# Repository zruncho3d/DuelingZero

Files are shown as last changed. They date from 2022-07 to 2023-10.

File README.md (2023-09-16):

## Dueling Zero - a Dual Gantry V0 mod

**Two extruders.  No compromises.**

Enable dual-color, dual-material, and dual-part printing... with the same speed and quality as single-extruder printing.

Mod a [Voron Zero](https://vorondesign.com/voron0.2) or build one fresh!

**D0** is the only open-source, fully-documented, reproducible-by-anyone Dual Gantry printer out there.

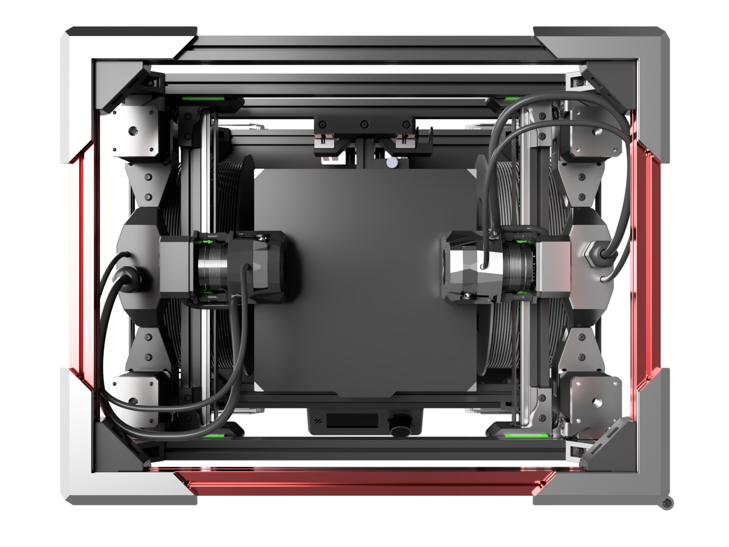
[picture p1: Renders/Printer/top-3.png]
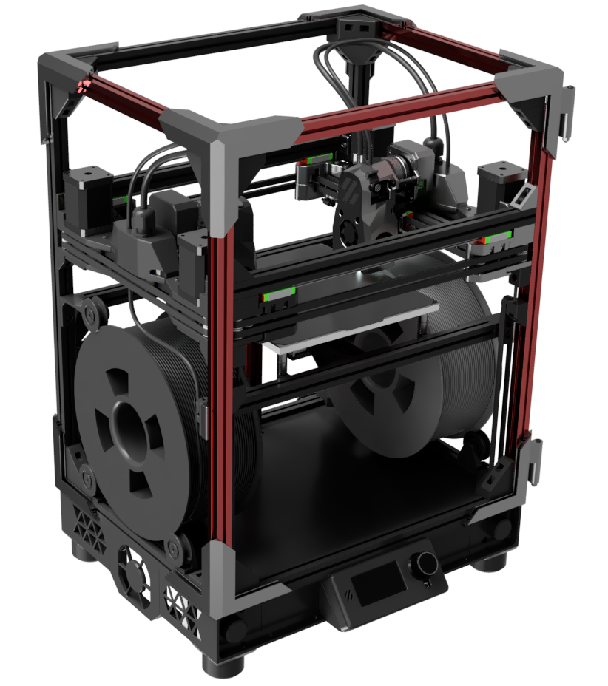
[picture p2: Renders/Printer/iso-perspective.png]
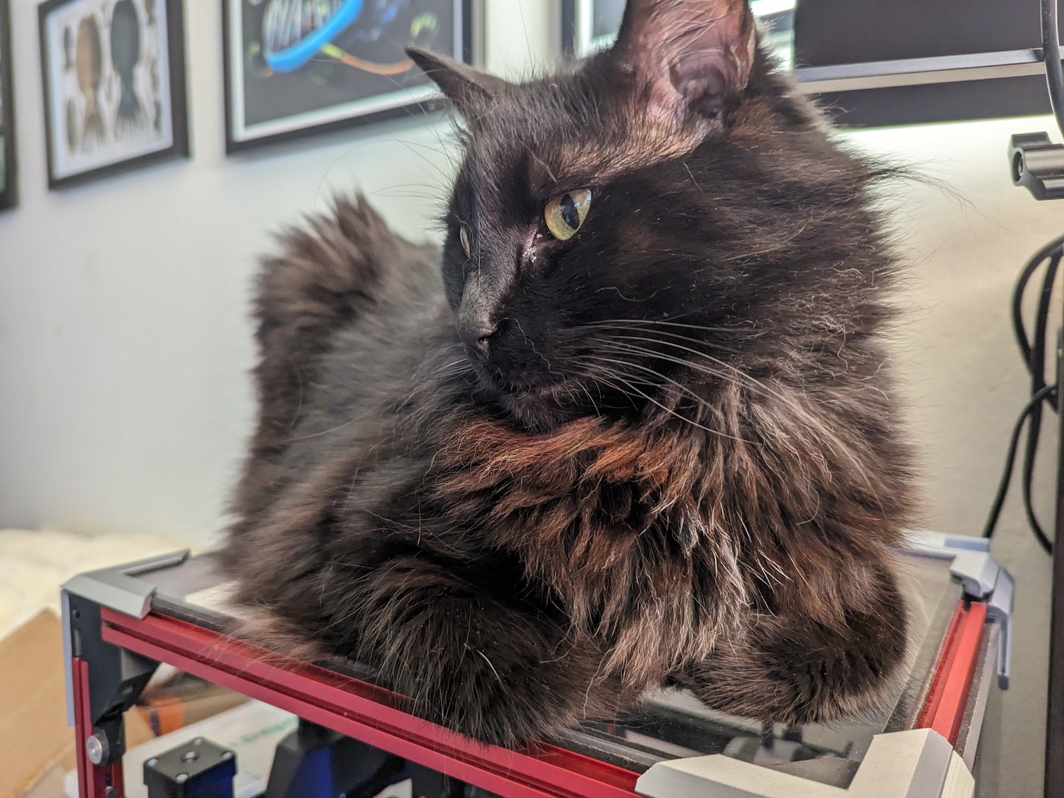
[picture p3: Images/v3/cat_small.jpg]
|  |  | 
| - | - | - |

In a Dual Gantry printer, the two heads are *fully* independent.  With **no extra weight** to drag around (vs an IDEX printer), and **no complexity added** to switch between heads (vs a toolchanger), Dual Gantry is a promising way to do more with a 3D printer.

Curious?  Watch the first one print below!

# [> > > Watch Video from first prints](https://youtu.be/2YI3_g30EwA)

(https://youtu.be/2YI3_g30EwA)
(original v1 gantry shown)

## What's Here?

Tons of content.  On this page:

- #### [Releases](#releases): Visual release notes
- #### [Overview](#overview): Why Dual Gantry?
- #### [Sample Builds](#samplebuilds): Parts and sizes
- #### [Links](#links), [Credits](#credits), and [Support](#support)

... and beyond, split into their own pages:
- #### [Parts](PARTS.md): Parts list to build your own
- #### [Instructions](INSTRUCTIONS.md): Instructions to print, assemble, and configure
- #### [Software](SOFTWARE.md): Two toolheads in one workspace, explained
- #### [FAQ](FAQ.md): Common questions, answered
- #### [Archived v1](Archived-v1/REAMDE-v1.md): Prior design

**Enjoy!** I hope this project inspires you to build something new, whether a D0 or your own design.  -Z

## Releases

**2023-09-16 v3 Gantry release and updates**

This release moves to a completely-new, symmetric, nested belt path:

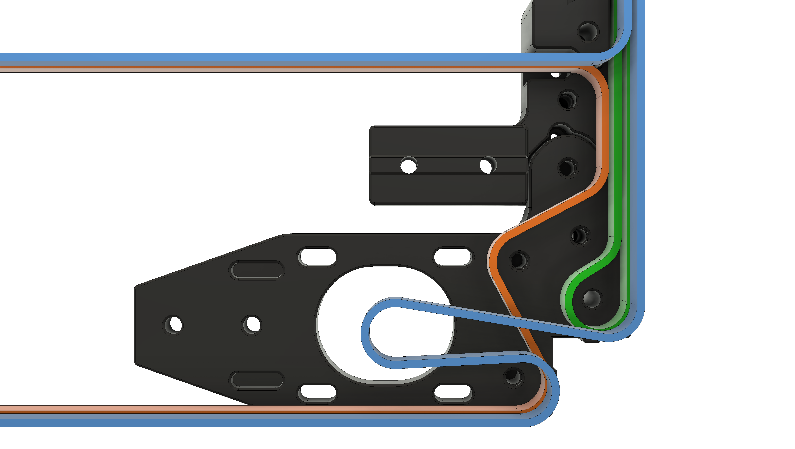
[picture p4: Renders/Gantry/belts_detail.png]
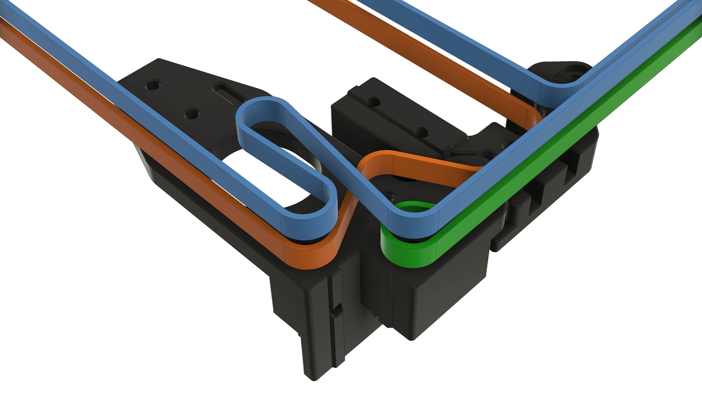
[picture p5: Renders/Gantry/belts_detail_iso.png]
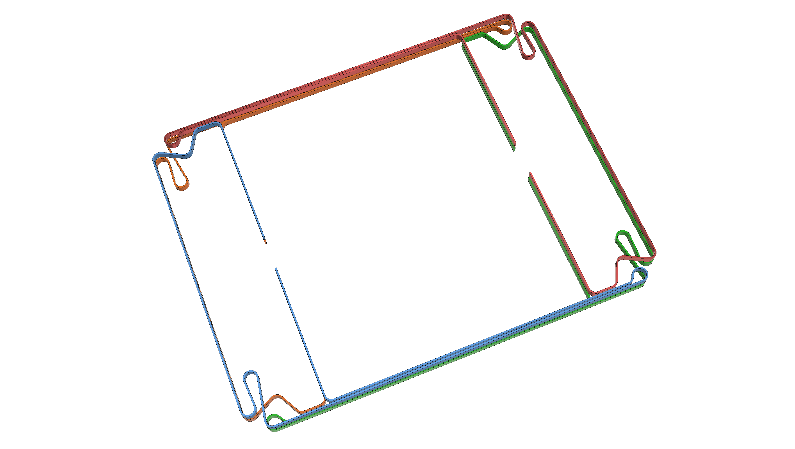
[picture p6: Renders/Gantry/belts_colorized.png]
|  |  |  |
| - | - | - |

The new [Pandora's Box](https://github.com/MasturMynd/Pandoras_Box/tree/main)-derived gantry design, created in close collaboration with `Desune` on Discord, has far fewer unique parts, adds travel, and enables wider toolhead compatibility.

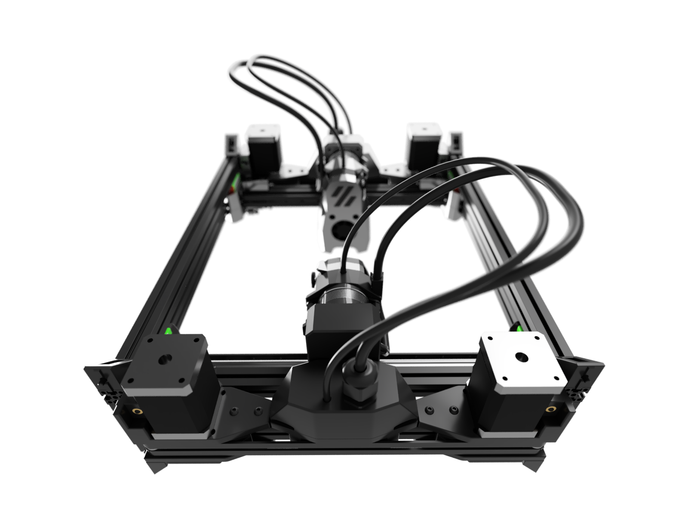
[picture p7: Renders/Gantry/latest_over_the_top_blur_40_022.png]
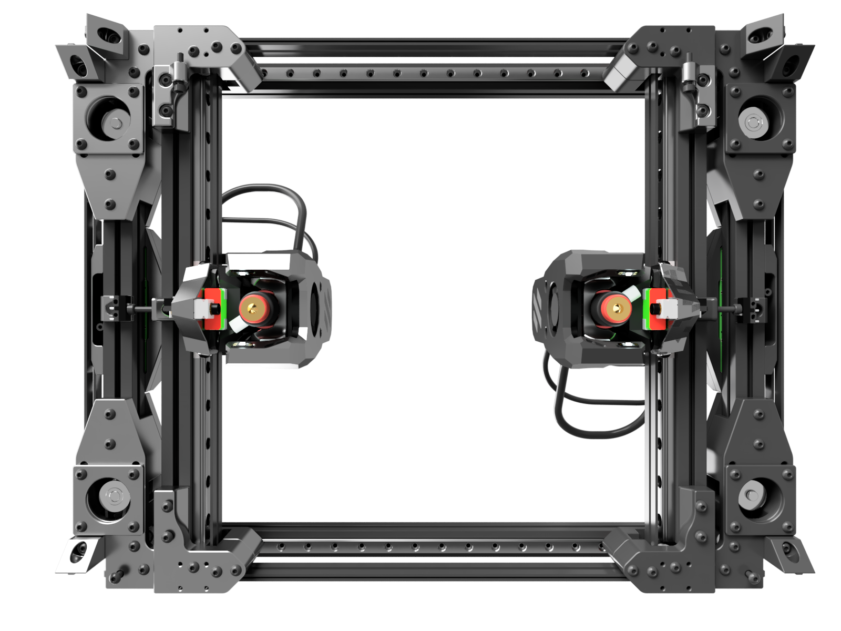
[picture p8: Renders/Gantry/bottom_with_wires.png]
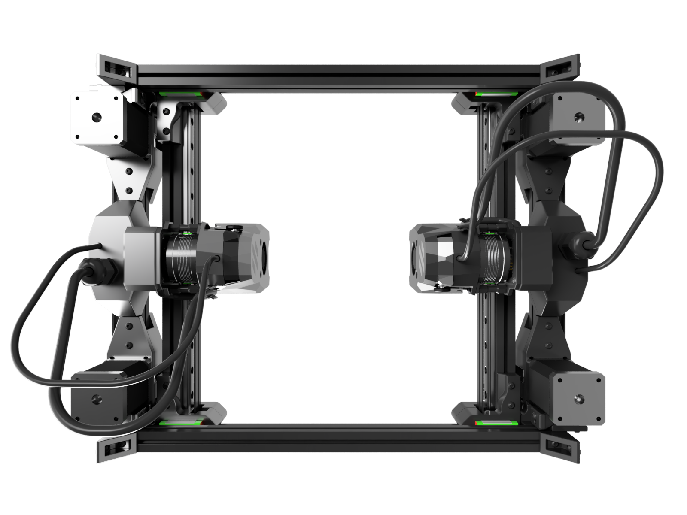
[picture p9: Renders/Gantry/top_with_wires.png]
|  |  |  |
| - | - | - |

Here's the side-by-side comparison from above, with v1 on left, and new v3 on right:

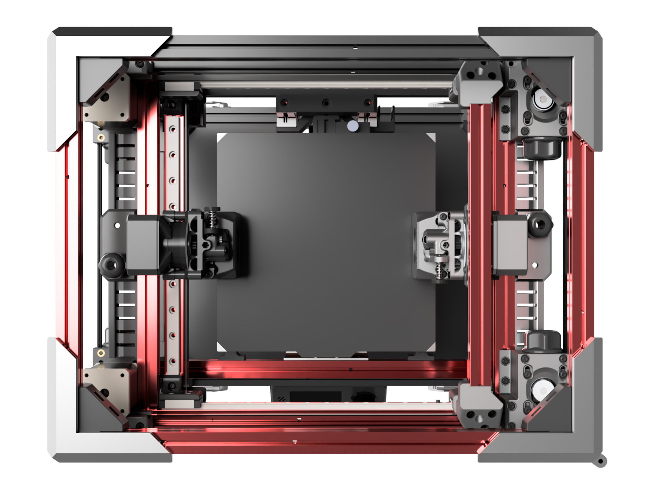
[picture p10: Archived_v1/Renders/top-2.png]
|  |  |
| - | - |

Or, in reality:

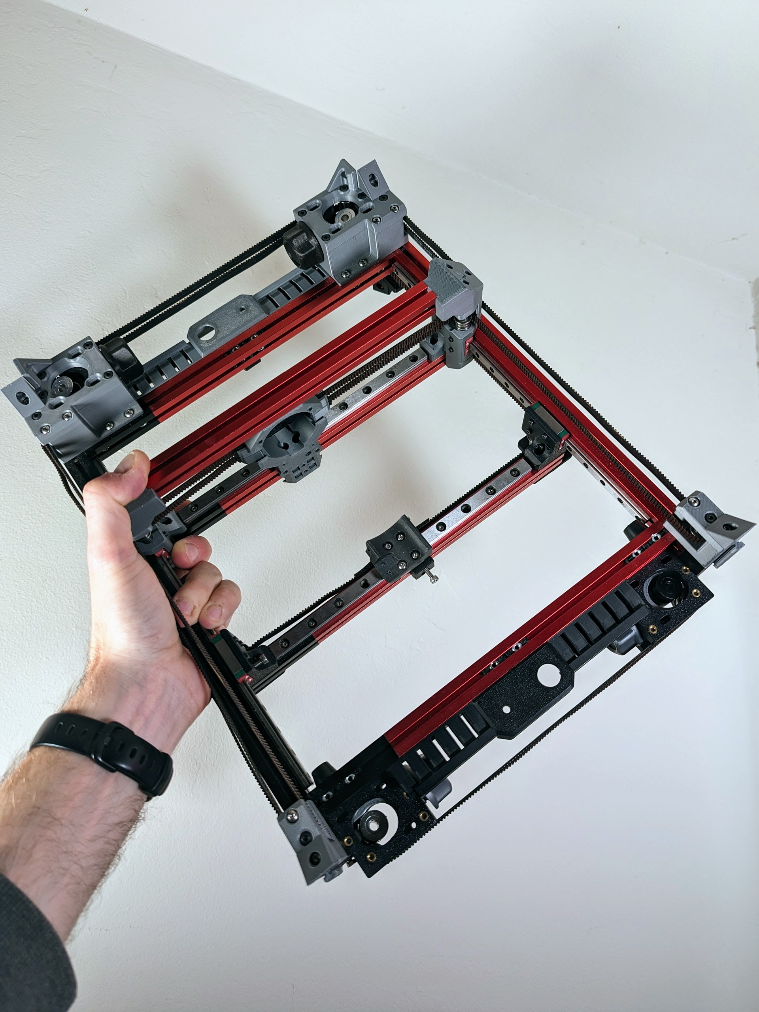
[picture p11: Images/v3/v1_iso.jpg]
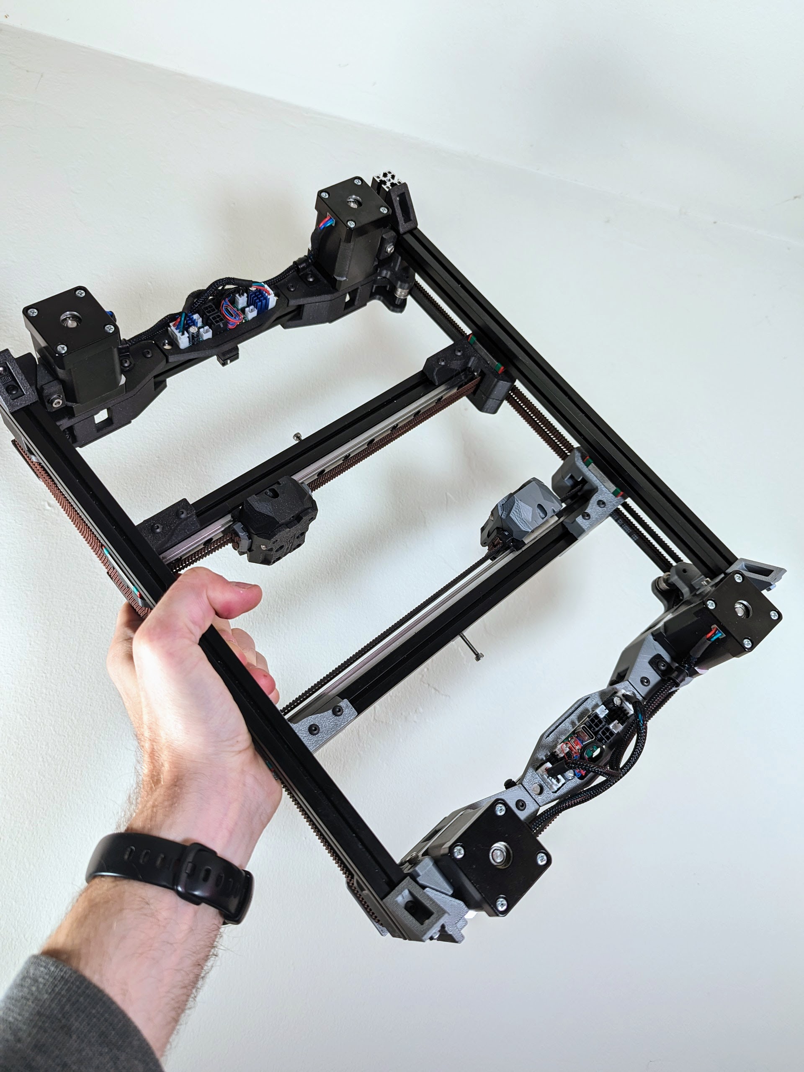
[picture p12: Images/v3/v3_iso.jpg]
|  |  |
| - | - |

The printer looks a little different now, with internal spool holders!

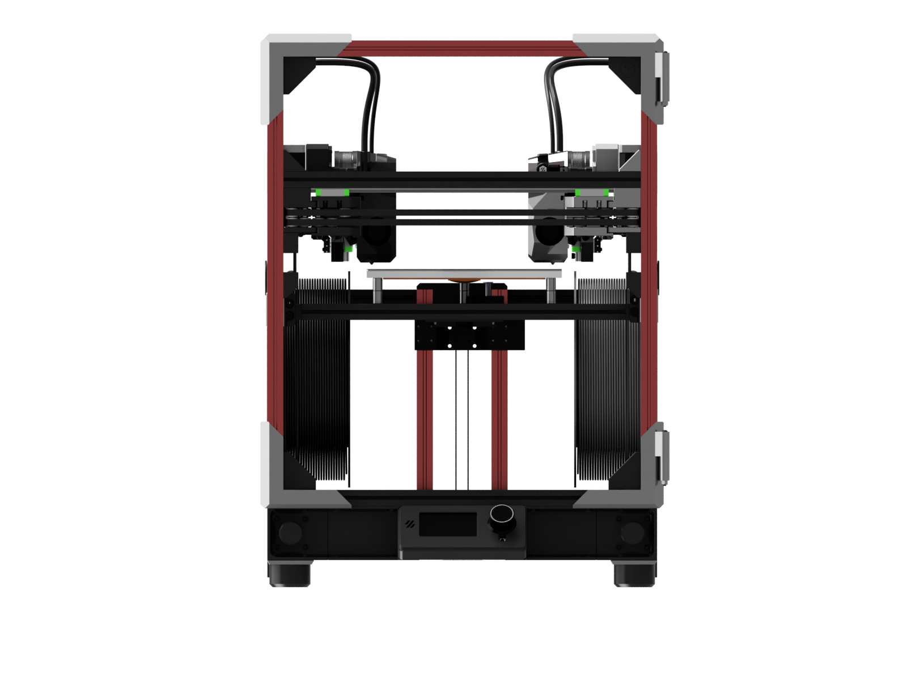
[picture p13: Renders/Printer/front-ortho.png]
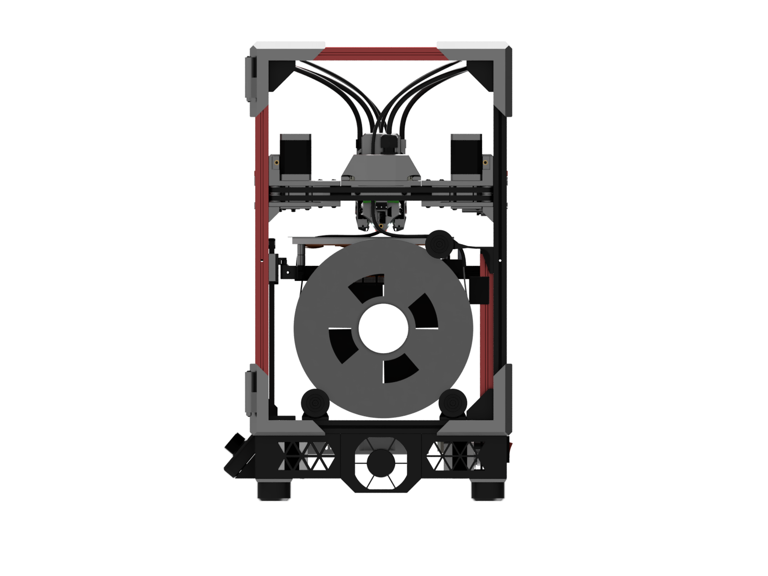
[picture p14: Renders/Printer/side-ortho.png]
|  |  |  |
| - | - | - |

In short - **this is a big update**.  *This is what D0 should have always been.*

Sometimes it's only through iteration and collaboration that you get to what feels right.  **The v3 gantry feels right**. No weird strut, no flipped motors, smaller, more maintainable... all-around, better.  See the comparison table on the [Design](DESIGN.md) page for more details on why.

Other improvements:
* **Boop support** for perfect first layers every time, nozzle probing with [Boop](https://github.com/PrintersForAnts/Boop) is now the default.  There are no magnets to get loose in a heated chamber and no probe motions to configure anymore.
* **Better toolhead compatibility**, including a Voron 0.2-compatible mount for the Voron Mini Stealthburner toolhead and many others.
* **Gantry board support** for the [GBB15 gantry board](https://github.com/skuep/GBB15) - enables super-clean, easy wiring with magnetic-attach covers.
* **Dual internal spool holders** added, reducing the effective width.

**Existing v1 builders**: to upgrade, the main costs will be new rails, a few new extrusions, and Boop parts.  There's nothing wrong with your v1 build; it will print fine.  But  if you want more travel and the benefits of Boop, a fresh rebuild with the new larger default frame size might make sense.

**For earlier releases**, see the [Updates](updates.md) page.

## Overview

### What’s a Dual Gantry printer?

**Dual Gantry** is a rare 3D printer type with two toolheads moved by **two** *completely independent* XY motion systems:

 

Yes, you’re seeing double, with black and silver toolheads in a dual-CoreXY motion configuration.

### Why a Dual Gantry printer?

In general, a second hotend adds enormous flexibility - to support two colors, two materials (typically support + main), and two nozzle sizes, in one print, with no color-bleed issues, cross-contamination, or wasteful purging.  Sounds good, right!

Well, that second hotend, if mounted on a single toolhead, can get in the way of print quality, as it drools filament when not in use - and the toolhead is now custom. :frowning:

So along comes IDEX, short for Independent Dual Extrusion, which adds a second, independent toolhead on a shared axis (typically the X axis).  Sounds better, right?

No drool, plus something cooler: one printer can now print two identical parts simultaneously, in mirror or duplicate modes. :muscle:  (note: in theory; depends on firmware support)

Open-source IDEX designs include [Voron](https://vorondesign.com/)-derived ones, like [Zruncho](https://github.com/zruncho3d)’s [Double Dragon](https://github.com/zruncho3d/double-dragon), [Eddietheengineer](https://www.youtube.com/eddietheengineer)'s [Tridex](https://github.com/FrankenVoron/Tridex/), and [Ankurv](https://github.com/ankurv2k6)’s [IDEX Switchwire](https://github.com/ankurv2k6/voron_idex_switchwire).  There's also the [Muldex](https://github.com/3dprintingworld/MULDEX), and there's no shortage of commercial examples, too: [Sovol SV04](https://sovol3d.com/products/sv04), [FlashForge Creator Pro](https://www.flashforge.com/product-detail/flashforge-creator-pro-2-3d-printer), [BCN Sigma](https://www.bcn3d.com/bcn3d-sigma-d25/), [Jadelabo J1](https://www.jadelabo.com/), and many more.

But that second toolhead comes at a cost: moving mass, which has effects on print speed (max accel) and quality (typically, ringing artifacts).  :neutral_face:

> Simplify, then add lightness - [famous quote from Colin Chapman at Lotus](http://www.lotuscars.com.tr/about-us/lotus-philosophy/index-31332.html#:~:text=At%20the%20root%20of%20our,was%20another%20of%20Chapman's%20premises.)

Whether building a fast race car or a fast printer, physics can't be ignored.  

You can mitigate the moving mass somewhat, by using a lighter toolhead, typically with a remote Bowden extruder, but Bowden extruders introduce their own tuning challenges.

**With Dual Gantry, you get a no-mass-added gantry for the common case of single-extruder prints.**  Unlike an IDEX, here, each toolhead is *truly independent* and can move in X *and* Y on its own - [potentially to print two completely different objects at once!](https://forum.duet3d.com/topic/27895/beta-testers-for-multiple-motion-system-support)

There’s no hit to max acceleration or potential for ringing caused by dragging around a heavy second toolhead on a longer rail all the time.

Sure, you can't print more than two colors, like a multi-material unit or toolchanger can, but everything in engineering is tradeoffs... and Dual Gantry is an interesting and new point in the broader space of 3D printer types that support multiple extrusion:  

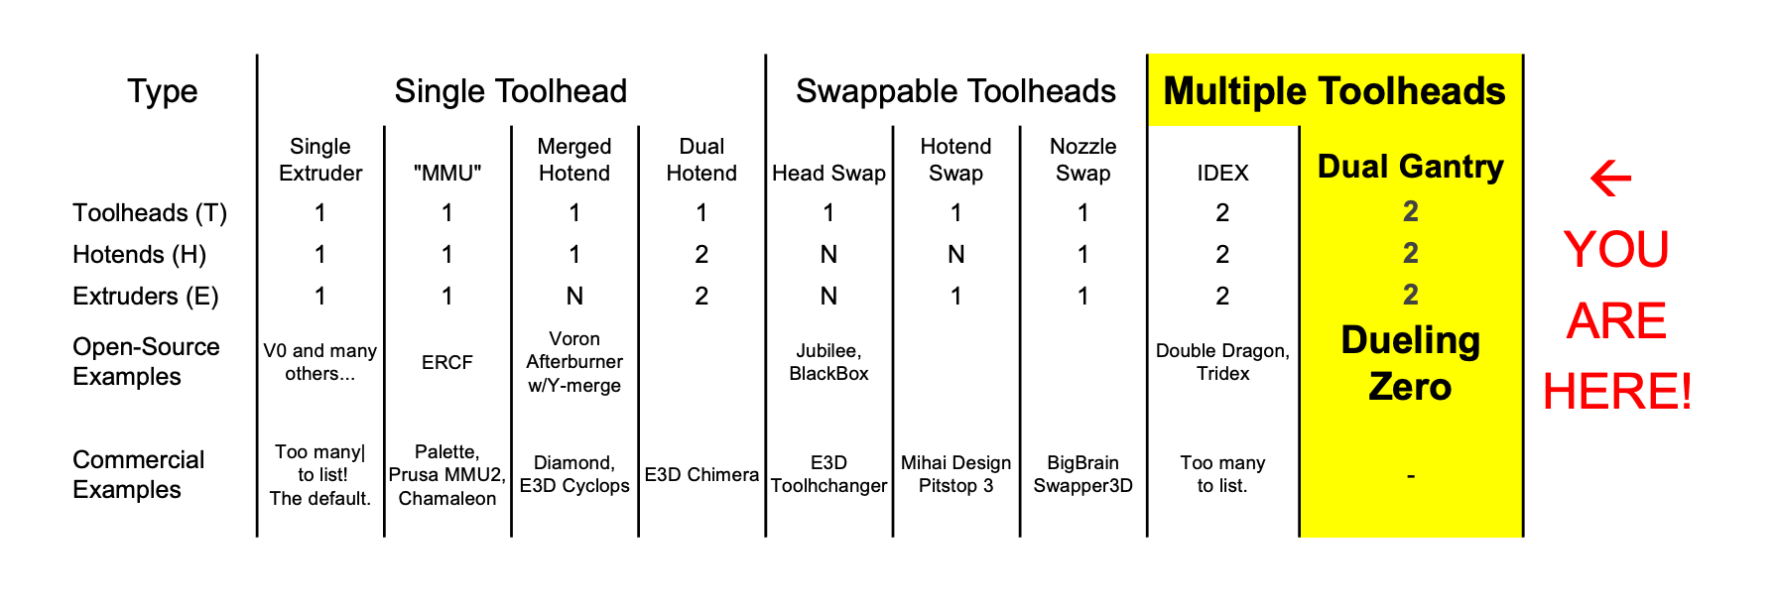
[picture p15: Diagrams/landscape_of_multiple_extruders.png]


Take a look at the table above, or at [this other helpful categorization](https://gist.github.com/kmcallister/6636d88802ba00432c65d14e9431c0e6).  This diagram is not comprehensive, but gives a sense for the depth of the design space, and especially, the rarity of everything not on the far left side (typical single-extruder printer).  For some interesting points in the design space, there's only one commercial example!  

(Please file an issue on GitHub if you know of any significant omissions.)

### What’s the catch?

On the plus side, you don't have to design it (anymore).  You don't need to program the firmware either (anymore): Klipper works (thanks to a collaboration with [tircown](https://github.com/tircown)) and RepRapFirmware supports two active gantries, out-of-the-box.  The software base needed to make full use of the workspace, by implementing collision detection and avoidance, is the `src` folder here and explained in the [Software](SOFTWARE.md) section.

On the minus side, building it is roughly twice the work of a typical printer.  There are added costs from the second gantry and toolhead.  There are alignment challenges - including XY and YZ skew calibration - which are currently unknown.  And like any multi-head printer, you'll have more tuning and slicer stuff to figure out.

If all that sounds daunting, this is not the printer for you.  If being the first to figure these out sounds exciting, this may be your next printer!

### How does this mod work?

Roughly... start with a Pandora's Box gantry.  Turn it 90 degrees.  Add extra bearing stacks and combine idlers with AB blocks.  Duplicate it about the center.  Flip it upside-down.  Add off-the-shelf Boop and toolheads.

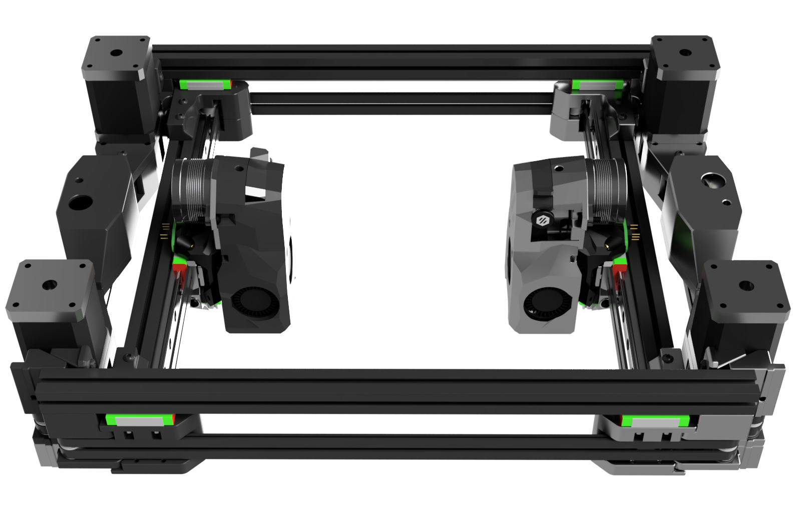
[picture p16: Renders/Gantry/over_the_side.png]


That’s the core idea.

In practice, though, there are quite a few additional bits to design to make it work.  And like any V0 mod, the devil is in the packaging details: *every mm matters*.

Beyond the gantry, D0 heavily leverages off-the-shelf parts from these repos:
* [BoxZero](https://github.com/zruncho3d/BoxZero) ditches the V0 tophat
* [TriZero](https://github.com/zruncho3d/tri-zero) adds automatic bed leveling and enables XY scalability from a fully-supported bed
* [ZeroPanels](https://github.com/zruncho3d/ZeroPanels) add snap-in, quick-release panels
* [Boop](https://github.com/PrintersForAnts/Boop) adds highly accurate nozzle probing
* [Voron V0.2](https://vorondesign.com/voron0.2) provides a good toolhead default

If you're not familiar with these mods, here's a pic, showing a Plus50-size Tri-Zero + BoxZero printer (170x170 bed motion), next to a V0-size (120x120 bed motion) Tri-Zero + BoxZero.  Both have ZeroPanels.

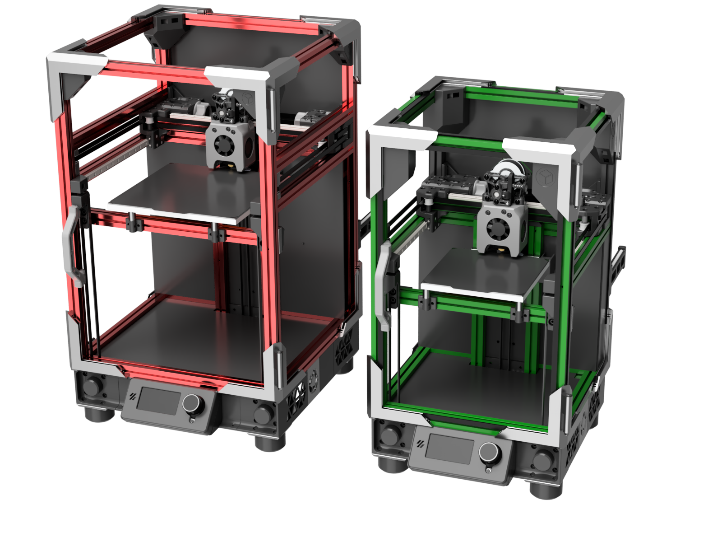
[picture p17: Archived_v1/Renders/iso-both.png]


## Sample Builds

Let's be honest here... there's no such thing as a completely "stock" D0 build.  If you can build this, you're going to pick the best parts for you, and the beauty of living within the V0/T0/Boop ecoystem - more than ever with the v3 gantry - is that you *get* this choice.

Two sample builds below should get you thinking.  Make sure to check out `Hex-Zero` mod by Alexander Þór (on the DoomCube Discord) and HBO's [T0 mods repo](https://github.com/harry-boe/tri-zero/tree/main/Mods/hbo) for alternate skirts and the Z joints, in particular.  Also check out Desune's [Dueling Boops](https://github.com/desune2487/Dueling_Boops) repo for alternate skirts and gantry parts.  For the latest, check `#dueling-zero-dev` on the DoomCube discord.

### Zruncho's Red/Black Build

Originally [V0.562](https://www.reddit.com/r/voroncorexy/comments/odfid1/voron_00_serial_request_zruncho1790/), then the first Dueling Zero, and now with the v3 gantry:

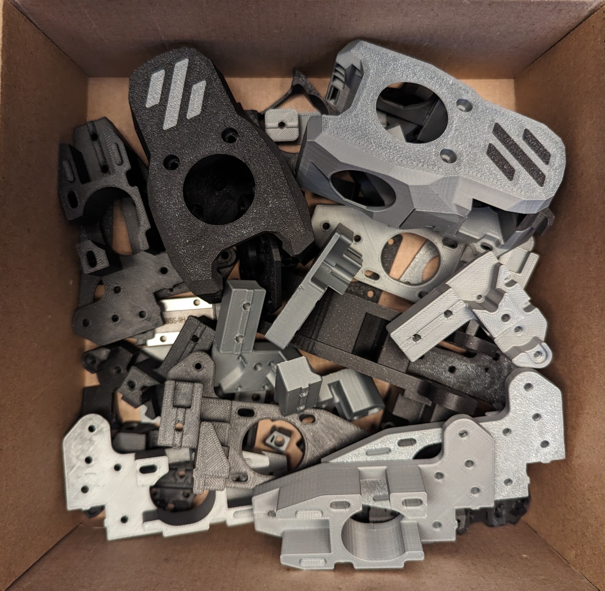
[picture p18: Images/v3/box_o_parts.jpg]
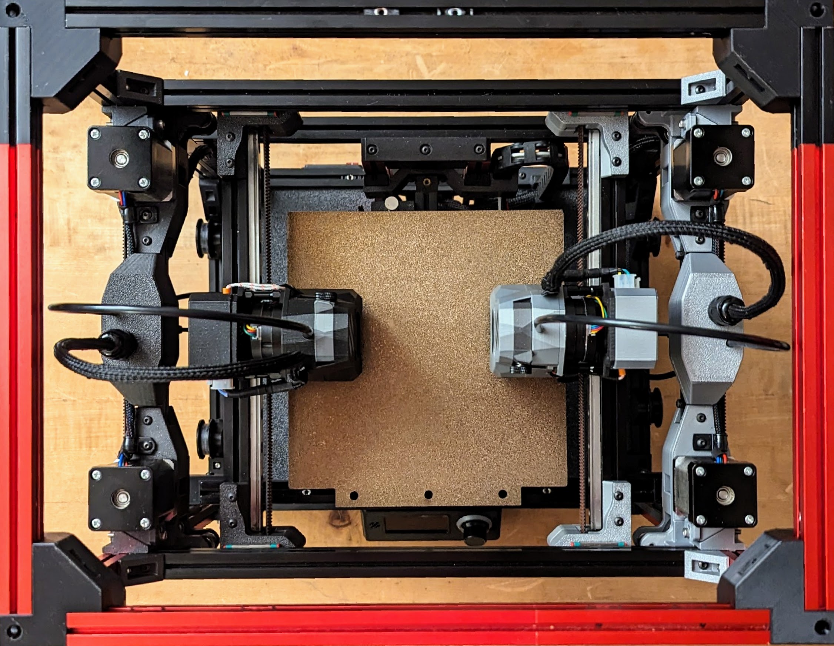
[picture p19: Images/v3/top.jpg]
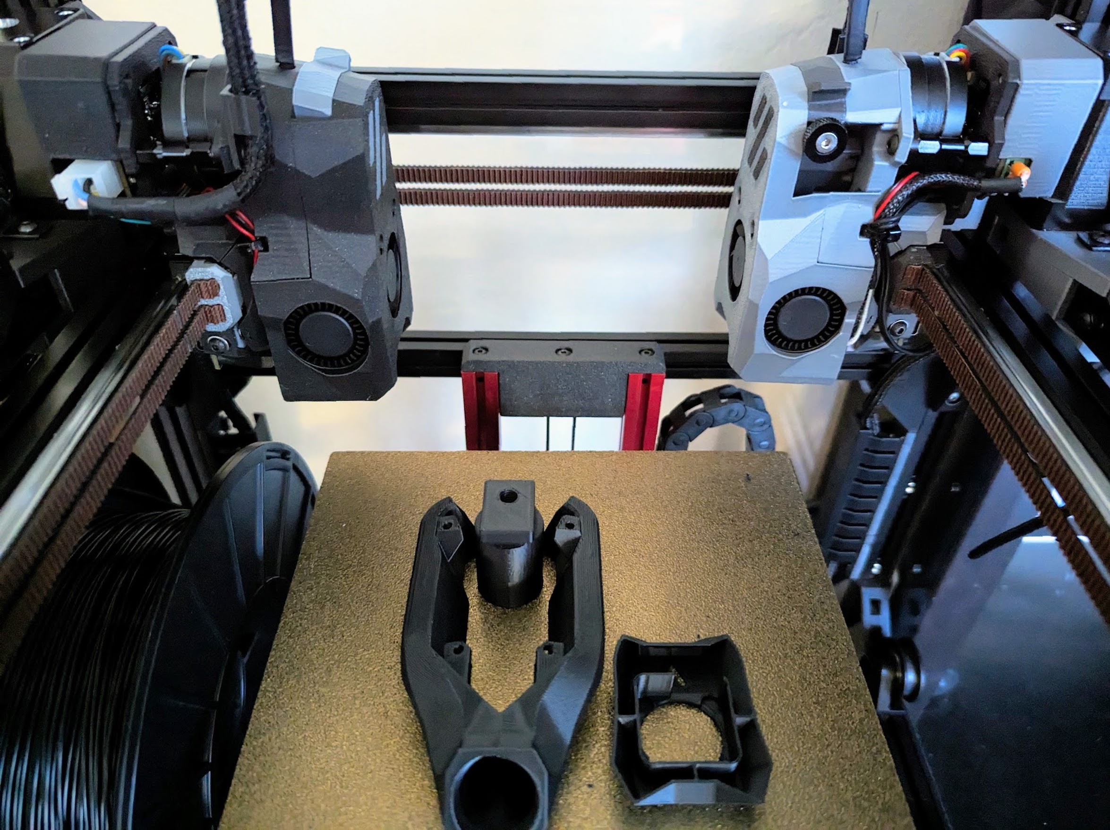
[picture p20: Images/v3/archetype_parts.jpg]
|  |  |  |
| - | - | - |

Highlights of this particular build:
* XY Motion and Toolhead
  * 2x [Boop beta-4](https://github.com/PrintersForAnts/Boop/tree/main/beta_4)-based carriages with nozzle bed probing, plus rear threads for toolhead boards, using the same sensor option as Tap
  * 2x [MiniSB](https://github.com/VoronDesign/Voron-0/tree/Voron0.2r1/STLs/Toolheads/Mini_Stealthburner) toolheads
  * 2x [Revo Voron](https://e3d-online.com/products/revo-voron) hotends - V0.2r1 version
  * 4x StepperOnline Nema 14 (14HS20-1504S) stepper motors
* Frame and Z
  * Rail-less Z motion (!) using printed Tri-Zero MGN7-compatible sliders with match fit to extrusions
  * [Tri-Zero](https://github.com/zruncho3d/tri-zero) triple-belted Z with tool-less belt attachments
  * 3x Kysan 1124090 NEMA17 motors for Z
  * LDO 1515 V0 frame kit (Red) + MakerBeamXL 1515 (Black) w/500mm pieces cut to size
  * 300W AC 180x180 [Prusa Mini size plate bed](https://www.aliexpress.com/item/3256803530287164.html) with textured and smooth PEI sheets
* Electronics
  * Raspberry Pi 3B
  * SKR Pico controller boards for Z motion
  * 2x [GBB15](https://github.com/skuep/GBB15) gantry boards
  * 2x EBB42 toolhead boards
  * BTT U2C USB CAN board
  * Meanwell LRS-150-24 PSU
  * Mini 12864 display with [Klipper adapter](https://www.aliexpress.com/item/3256802553287831.html)
  * 2x Fysetc PIS USB ADXL boards mounted to x carriages
* Other
  * Panels: [ZeroPanels v3](https://github.com/zruncho3d/ZeroPanels) with optional midclips and rear-hinged top panel
  * Travel: 166mm x 180mm in XY, ~130mm in Z (not optimized!)
  * Filament: mix of KVP ABS flavors: Metallic Silver, Black, and Stellar Black.
  * [PrinterExperiments](https://github.com/zruncho3d/printer-experiments) code for easy Z nozzle alignment with a single command

This build is a bit too small to cover the full bed and support over-travel in all directions. For all new builds, a build the size of Desune's is recommended; more in the [Parts](PARTS.md) section.

### Desune's Silver Build

Highlights of this particular build:

* XY Motion and Toolheads
  * 2x Boop beta4 with OptoTap v2.4.1 board (slightly modified for rear microswitch mounting)
  * 2x Dragon Burner v7 (modified for Boop clearance)
  * 2x Rapido v2 HF
  * 2x Orbiter v2 extruders with filament sensors
  * 2x MGN7H 300mm
  * 2x MGN9H 250mm
  * 4x StepperOnline Nema 14 (14HS20-1504S) stepper motors
  * 3x Cloudray Nema 17 (17CS04A) stepper motors
* Frame and Z
  * Misumi 1515 extrusions (silver)
  * Rail-less Z motion sliders (modified to fit Misumi extrusions)
  * Triple-belted Z with custom Pandora'sBox-derived GE5C joints
  * 180x180 bed with 300W AC powered heater
* Electronics
  * BTT Manta M8P v1.1 with CB1 v2.2 compute module
  * 2x BTT EBB36 v1.2 toolhead boards
  * 7x BTT TMC2209 stepper drivers
  * BTT TFT35 SPI v2.1 touchscreen
  * Meanwell UHP-200 PSU
  * CG 40A DA SSR
* Other
  * ZeroPanels clips (modified for screw mount on Misumi extrusions)
  * Filament - eSUN ABS silver and black
  * Removable base panel for easy electronics access.
  * Outer Dimensions (without enclosure panels):  L: 290  W:380  H:526mm   Height includes electronics compartment and feet.  Vertical extrusions are currently 450mm, however 50~100mm of extra height for umbilical clearance is recommended for maximum Z travel.
  * Maximum XY travel (approximate):  X:188mm  Y:194mm  (with Dragon Burner toolhead)
  * Maximum Z travel (as configured with 200mm linear rails): 168mm

The parts for this specific build are available at Desune's [Dueling Boops](https://github.com/desune2487/Dueling_Boops) repo.  They are extremely similar to Zruncho's parallel implementation; the two influenced each other during development.  Definitely take a look, as you can mix and match parts from this one, including the updated skirts and bed pieces.

### Learn more!

If you've read this far, great, but there's more good stuff.

There's lots more info beyond this README file, in the repo, split into multiple pages.  And the [V1 Archives](Archived_v1/) section provides a view into the original design that you might find interesting.

Take a look around, or back to the What's Here section above.

## Links

### Dual Gantry

They do exist!  Others have built printers or similar CNC devices with at least two gantries operating in a single shared workspace:

* [Essentium HSE 280i](https://www.essentium.com/3d-printers/high-speed-extrusion-280/): large, high-dollar, linear-servo printer with two gantries
* [Cronus](https://www.youtube.com/watch?v=TkEOMQ6rQ6s): a 5-head, single-workspace 3d printer
* [Dual Gantry CNC Machining Centers](https://www.cronsrud.com/cro-dual-gantry.html): a related CNC
* [Earlier motion platform example](https://www.youtube.com/watch?v=S_7VCEe3hOk): dates to 2012!

There are also a bunch of posts online with people conceptualizing the concept, dating back years.  The benefits/drawbacks are relatively straightforward to understand, though not widely known.  For a few builds, there are mentions online, but no reference to a video of the machine printing, or a link to learn more.

* 2018-06-04 [Duet Forum post by 3D_low](https://forum.duet3d.com/topic/5561/did-anyone-make-a-idex-with-dual-x-gantry-bar): "Did anyone pull that off yet? i havent found one on the net."
* 2018-11-21 [Duet Forum post by Haggan90](https://forum.duet3d.com/topic/7796/haq-xy/122): HaqXY is a dual Hybrid-CoreXY
* 2021-03-01 [r/3Dprinting post by u/m47812](https://www.reddit.com/r/3Dprinting/comments/lv8ksv/developed_a_new_kind_of_dual_extruder_system_on/): "CODEX" project.  Video shows a fairly far-along dual-gantry; describes collaborative mode too.  Abandoned as of 2023 in favor of a toolchanger.
* 2021-05-01 [r/Reprap post by u/lowfat](https://www.reddit.com/r/Reprap/comments/n2tkvb/corexy_with_dual_fully_independent_gantries/): postulates DG, but abandoned in favor of a toolchanger
* 2021-07-21 [Duet Forum post by breed](https://forum.duet3d.com/topic/24258/independant-dual-gantry-corexy/10?_=1657058082320): "Independent Dual Gantry CoreXY"
* 2021-09-17 [Duet Forum post by oliof](https://forum.duet3d.com/topic/25158/core-xy-idex-with-two-gantries/15): "Core XY - Idex with two gantries", has a nice diagram
* 2022-01-27 [Klipper Discourse post](https://klipper.discourse.group/t/dual-gantry-printer-with-single-mcu-btt-gtr-btt-m5/1900): Dual gantry printer with single MCU
* 2022-03-25 [Duet Forum post by dc42](https://forum.duet3d.com/topic/27895/beta-testers-for-multiple-motion-system-support/41): Beta testers for multiple motion system support: simultaneous multi-printing for RRF v3.5.  Note two pictures, for motion designs from breed and slaughter2k
* 2022-06-23 [Duet Forum post by zruncho](https://forum.duet3d.com/topic/29023/independent-dual-gantry-any-examples-out-there/10): is anything out there?

Please raise an issue for this repo to update the list of links if you come across one!  There’s no pretense of true originality here.

### Related

* [Bill Deckingham’s beast](https://www.youtube.com/watch?t=488&v=O_whcaAJpfs&feature=youtu.be): a CoreXYUVAB system, with extra axes for a very different reason.  Maybe some software lessons or relevant RRF config here?
* [Hashprinter](https://forum.duet3d.com/topic/24287/hash-printer-with-super-simple-gantry/2): super simple gantry
* TAMV = Tool Alignment with Machine Vision: a way to automate XY calibration
  * [Jubilee Toolchanger page](https://jubilee3d.com/index.php?title=TAMV)
  * [HaythamB fork](https://github.com/HaythamB/TAMV)
  * [TAMV on Klipper](https://github.com/TypQxQ/TAMV)
* [Klipper PR by Tircown that adds duplication and mirror modes](https://github.com/Klipper3d/klipper/pull/4464)
* [PitStop3](https://mihaidesigns.com/pages/pitstop-3-multi-material-3d-printer): hotend-swapping multi-material printer
* [Swapper3D](https://www.kickstarter.com/projects/bigbrain3d/swapper3d): nozzle-swapping multi-material printer
* [Enraged Rabbit Project](https://github.com/EtteGit/EnragedRabbitProject): add multimaterial capability
* [3D Chamaleon](https://www.3dchameleon.com/): automatic color changer

## Credits

* **Desune**: designed Dueling Boops (the honorary v2 gantry) and co-designed the v3 gantry w/Zruncho.
* **MasturMynd**: designed Pandora, which made this possible.
* **Tircown**: made a single-Klipper-instance version possible, with his code and live debugging
* **Clee**: saved the project with some hardcore hardware rescue with the STM GB01 chips
* **ToxGunn**: diagnosed a stepper overcurrent issue and saved me more plastic and motors
* **Reviewers**: thanks for providing feedback that helped make this clear and concise!
  * **v3: Caza, Kevinakasam, Tircown, Sanity, Telxoid**
  * **v1: Red5, _xbst, where’sthelambSAUCE, BeastBc**
* **Clee, Red5, Kyrios, Leopard, EddieTheEngineer, and others**: initial conversations proved motivating - that this wasn’t completely insane.  Thanks!
* **Nemgrea**: none of this would have happened without a solid base.

## Support

The best place to ask questions and see the latest is on the DoomCube Discord, where many Printers For Ants builders hang out.  Go to the `#dueling-zero-dev` thread in the #tri-zero channel.  Put your build log in the `#build_logs` showcase forum there too!

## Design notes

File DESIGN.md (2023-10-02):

The gantry improvements are summarized below:

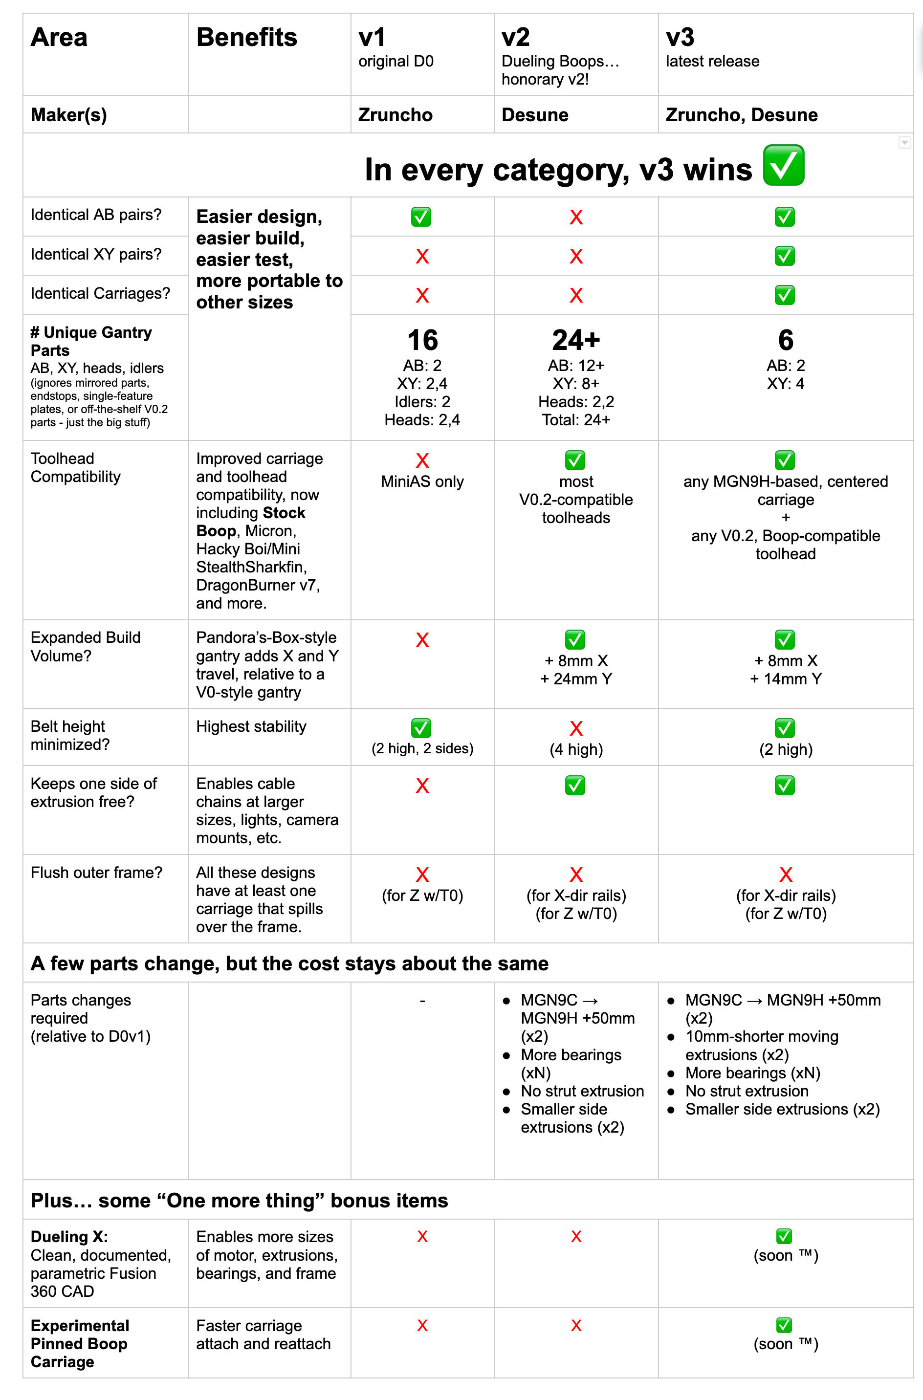
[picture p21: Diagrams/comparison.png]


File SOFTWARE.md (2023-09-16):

## Software

This early video shows the motion and introduces the core challenge: two toolheads moving in a shared space.  I didn't know if it work would at all when this was made!

[Early video showing motion in a shared space](https://www.youtube.com/watch?v=kvWQ7X1aL_c)

There are a few ways to handle the "two toolheads, one workspace" challenge, for a single print.

Here are the different cases, visualized, with more details explanations below.

| Option | Visualization | Notes |
| - | - | - |
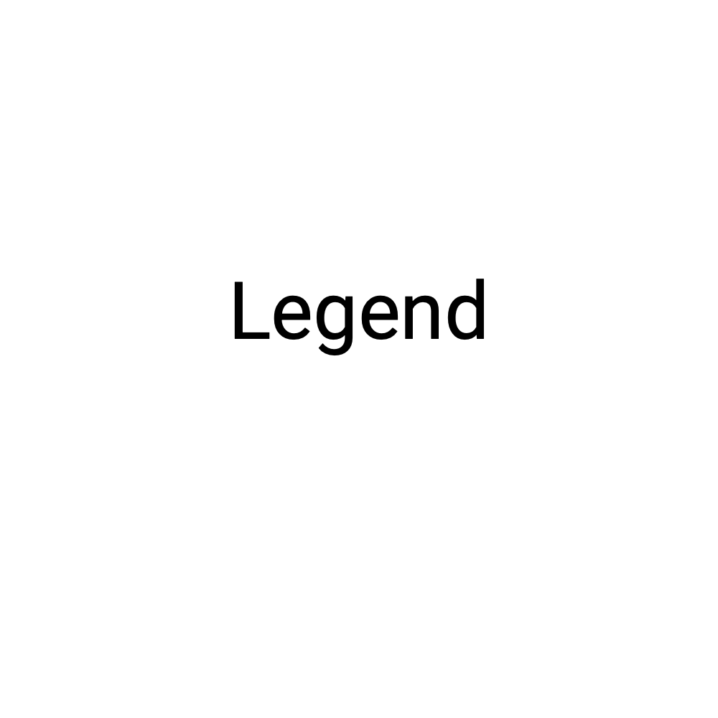
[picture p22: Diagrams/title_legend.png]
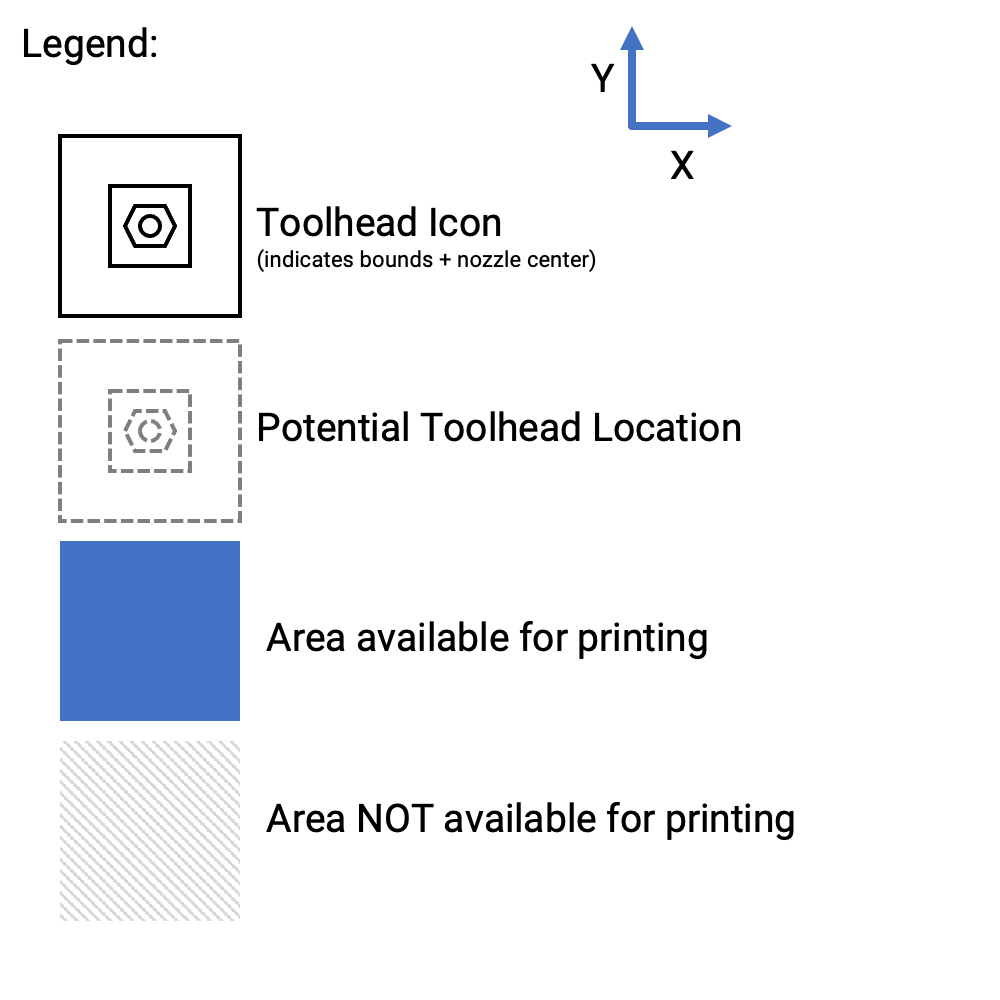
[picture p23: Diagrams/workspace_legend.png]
|  |  | - |
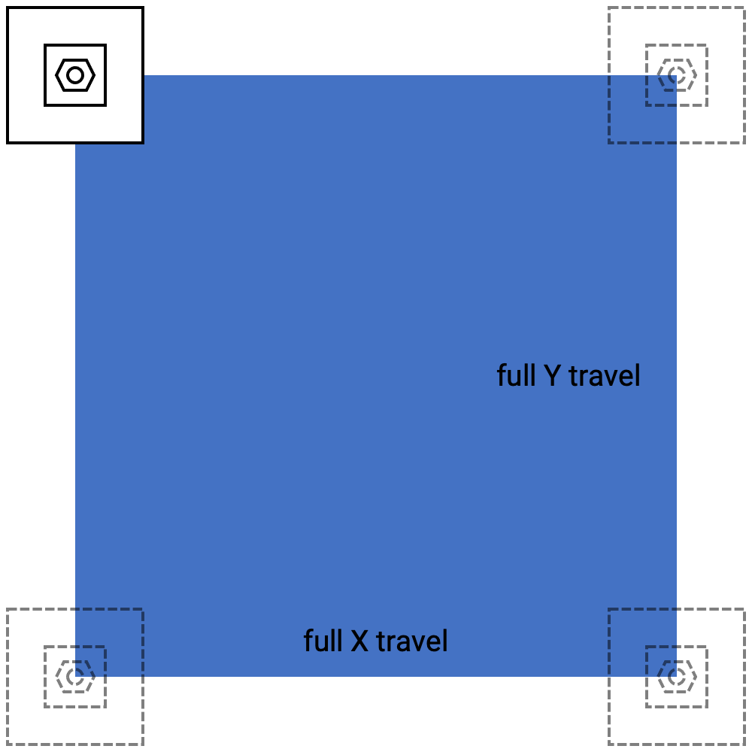
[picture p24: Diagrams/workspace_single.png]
| **Single Toolhead**: <p><p>Full Workspace <p><p> 100% travel |  | Ditch one of the toolheads, and Dual Gantry reduces to a single CoreXY. You can leave the inactive toolhead on and lose a corner of printable space, or you can remove the second toolhead to get nearly the full printable space. <p><p> If you mostly print in one color/material, this full travel is ... well, useful! <p><p> In a way, your daily driver for single-extrusion prints can also be the project car for the weekend (multi-material and multi-color).  But that’s not why we’re here, is it?|
|  |  |  |
| **Dual Toolhead Modes** without collision detection and avoidance (below) | | These modes works similarly to an IDEX, where a toolchange macro (typically `T0` or `T1`) parks the now-inactive toolhead, and motion then continues with the newly-active toolhead.  These methods can be implemented with simple toolchange macros, but firmware simplicity comes at the cost of some printable space.|
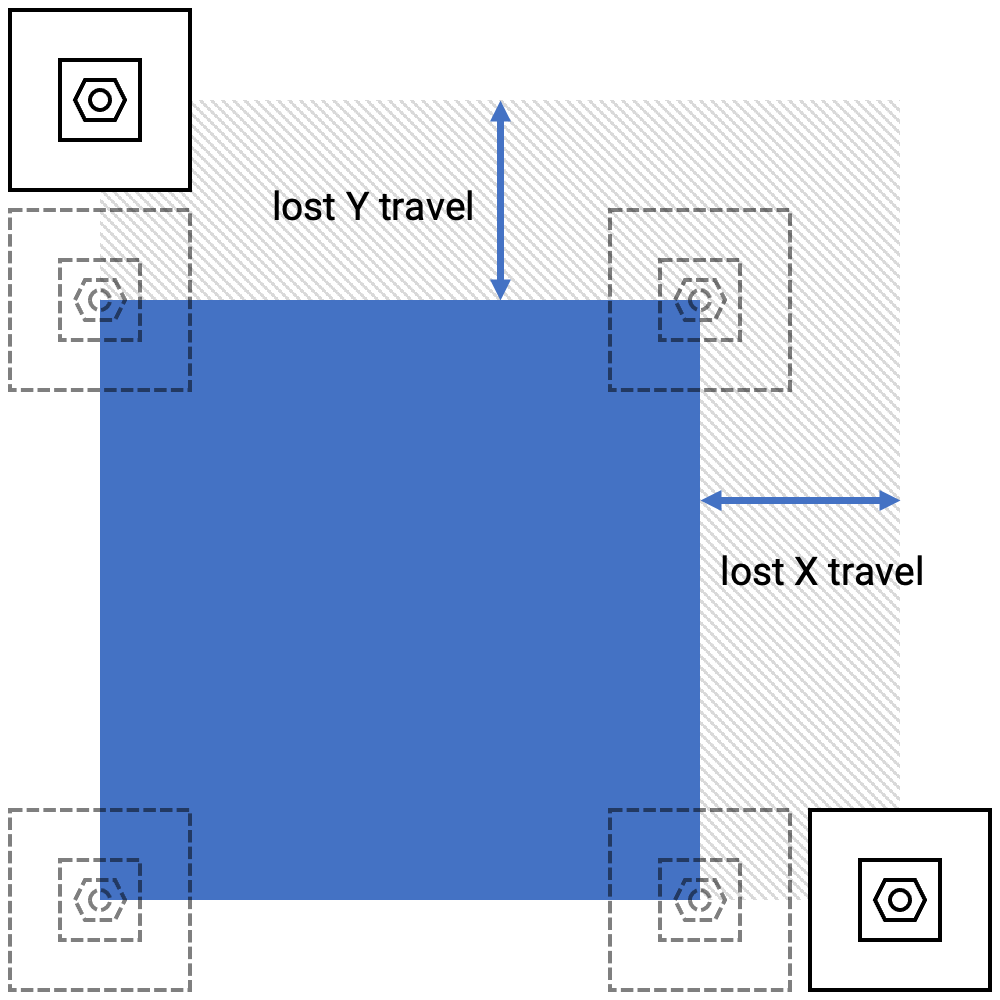
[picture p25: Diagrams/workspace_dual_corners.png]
| **Dual Toolhead**, Option 1: <p><p>Park in Opposite Corners <p><p> **49.7%** usable travel |  | Use the front left area, possibly with a regular V0 bed. You lose a toolhead's depth of X travel and a toolhead’s width of Y travel, yielding a nearly-square build area. |
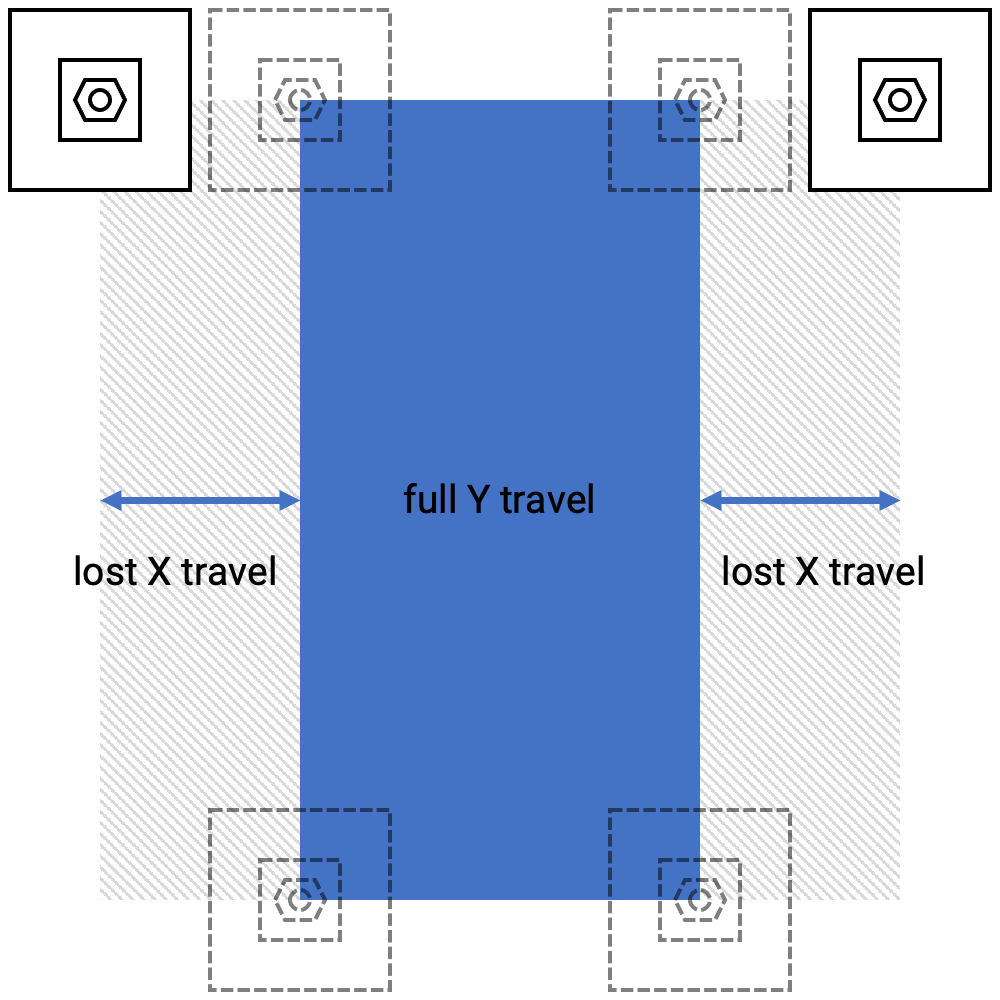
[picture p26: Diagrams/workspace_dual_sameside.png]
| **Dual Toolhead**, Option 2: <p><p>Park in Back, <p>Print in Center <p>  **47.1%** usable travel |  | Use the center area.  It’s just like an IDEX here; you lose twice the depth of a toolhead in the X direction, but retain full Y. |
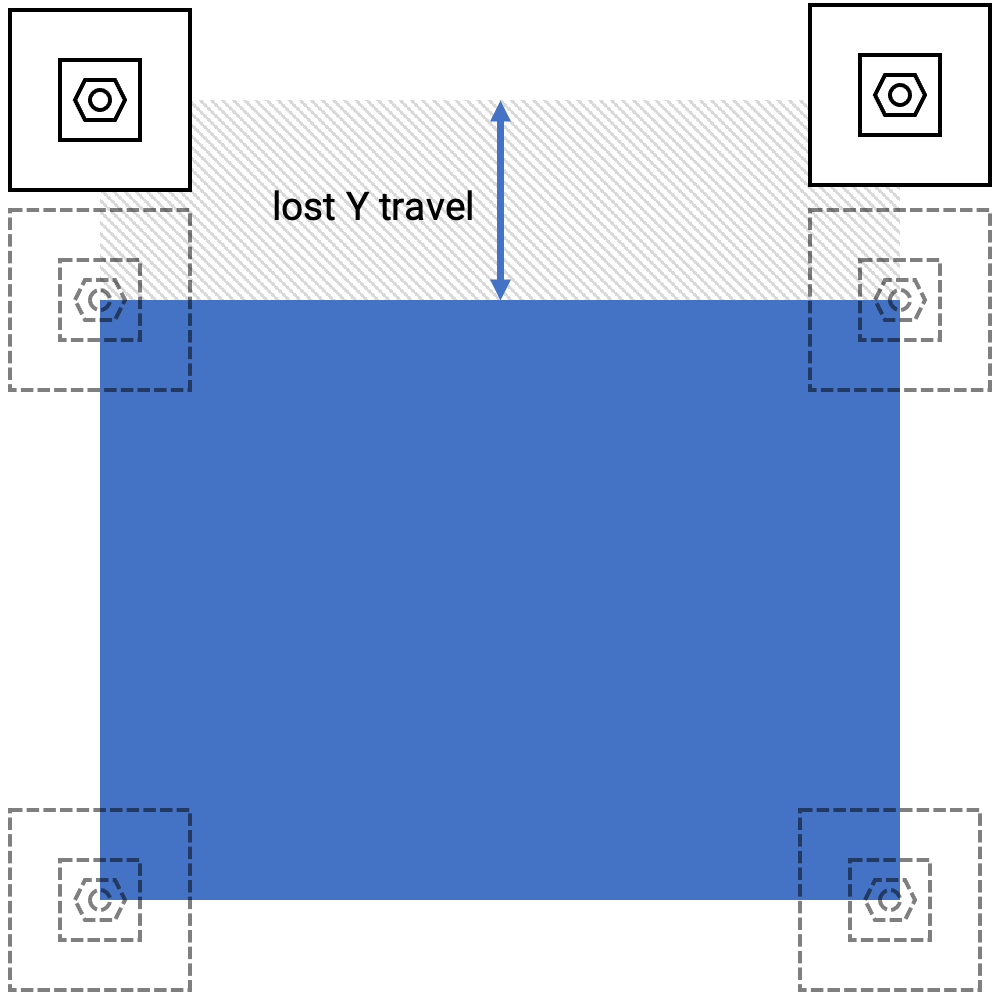
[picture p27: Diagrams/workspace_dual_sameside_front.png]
| **Dual Toolhead**, Option 3: <p><p>Park in Back, <p>Print in Front <p><p> **67.6%** usable travel |  | Use the front area, and leverage a gantry design that can overlap in X, for more printable space.  Requires toolchange macros to move the active gantry back into the workspace first. |
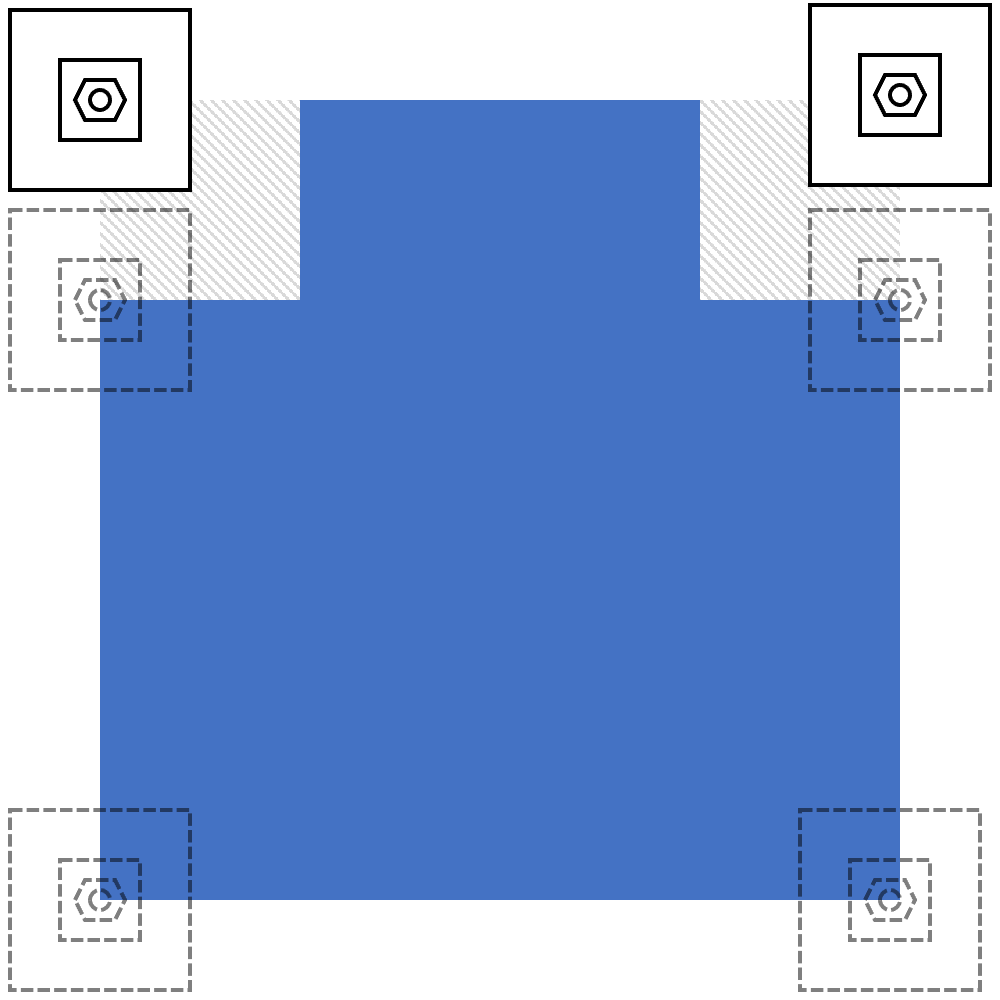
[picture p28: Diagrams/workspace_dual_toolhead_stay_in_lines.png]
| **Dual Toolhead**, Option 4: <p><p> Stay Within the Lines <p><p> **82.9%** usable travel |  | Use the front area in addition to the middle rear area, but assume each toolhead parks in a far corner.  <p><p> Requires a diligent slicer operator or the smart slicer itself to ensure that motion commands stay within the lines: cutting corners here could result in a collision.  Seems like a pretty-good option though. |
| | | |
| **Dual Toolhead Modes** *with* collision detection and avoidance (below) | | |
| **Dual Toolhead**, Option 5: <p><p>Interference Detection and Avoidance <p><p> **100%** usable travel |  | Ahhh yes.  Where it gets interesting! <p><p> For every travel move, some code must detect toolhead interference and proactively avoid it to use the full workspace. <p><p> **Read below for details.** |

It all makes me want to play some Tetris on a 1989 Game Boy, and play long enough to see a Buran take off again at the credits screen.

Anyway, for the calculations that drive the usable-travel numbers above, as well as V0 and V2 sizes, check [this spreadsheet](https://docs.google.com/spreadsheets/d/12tuhSCjSPbqNk4CZrzta5T9k3skF8ElGdcyRElUPhNI/edit?usp=sharing).

At smaller bed sizes, the simple options drastically reduce the usable bed size, motivating the use of interference detection and avoidance.  At larger sizes, there's less loss.  

Sure, you can always go "one size up" on the extrusions to get 100% usable bed fraction, by going with ~50mm wider X and Y extrusions and wider panels, and doing something simple, like *Park in Opposite Corners*.  But that means a larger, heavier printer, with more air to heat up, longer belt runs, and potentially more challenges with tuning.

If you can get 100% of the usable bed with software... why not use that?

### Interference Detection and Avoidance

**Ahhh yes.  Where it gets interesting!  Read on.**

For every travel move, some code:
* slicer
* G-code post-processor
* firmware

... must detect toolhead interferences and proactively avoid them in the full workspace.

Consider any G-code move command (`G0`, `G1`, `G28`, etc.), then ask this question:

> Would one toolhead (a ~40 mm x 53 mm rectangle in XY, plus some clearance) intersect with the other toolhead's rectangle, at any point in the motion for that move command?  

There are four distinct cases of motion here, at least when the toolheads are small relative to the travel.

An American football analogy will help us here.

| American Football Field | Dueling Zero Workspace |
| - | - |
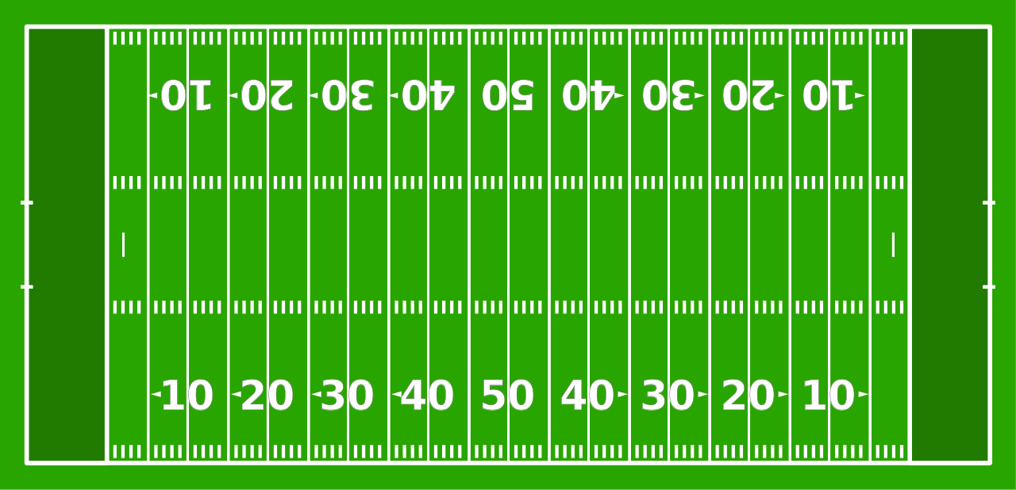
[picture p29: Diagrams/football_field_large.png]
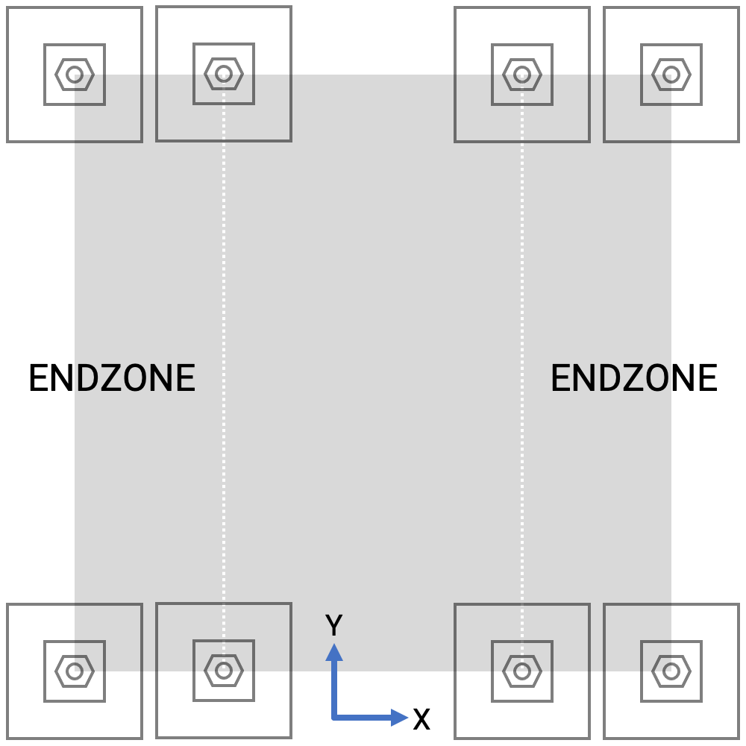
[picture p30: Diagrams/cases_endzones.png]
|  |  |
|  |  |
| The **"endzones"** are in the far X positions, on each side.  | An endzone begins where one toolhead would potentially collide with the other far-X-position toolhead. |

We'll walk through the four distinct cases.

| Case | Explanation |
| - | - |
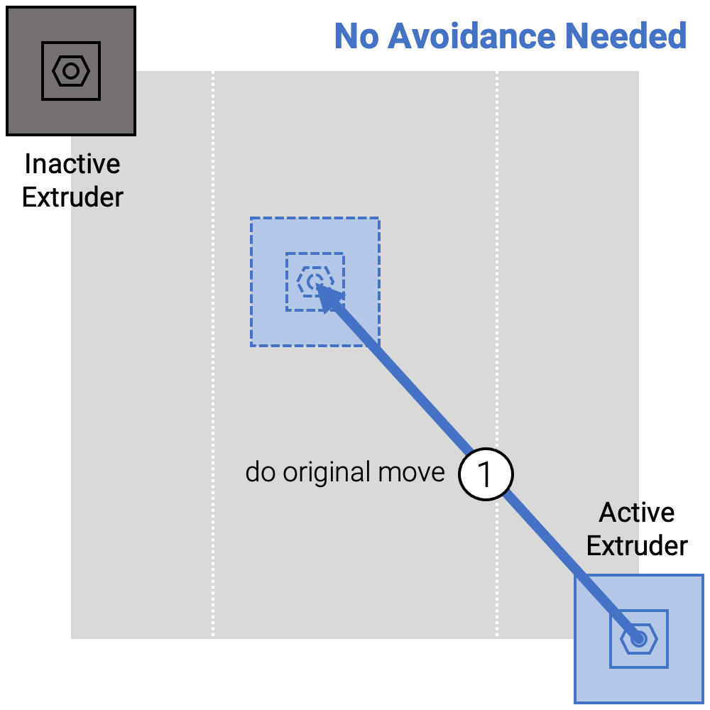
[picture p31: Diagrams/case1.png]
|  | **Case 1: No Avoidance Needed**<p><p>An interference can only occur if the move goes to a far X edge - to the endzone.  If the move doesn’t start or enter either endzone, and the inactive extruder is parked in the endzone, then nothing smart is needed. |
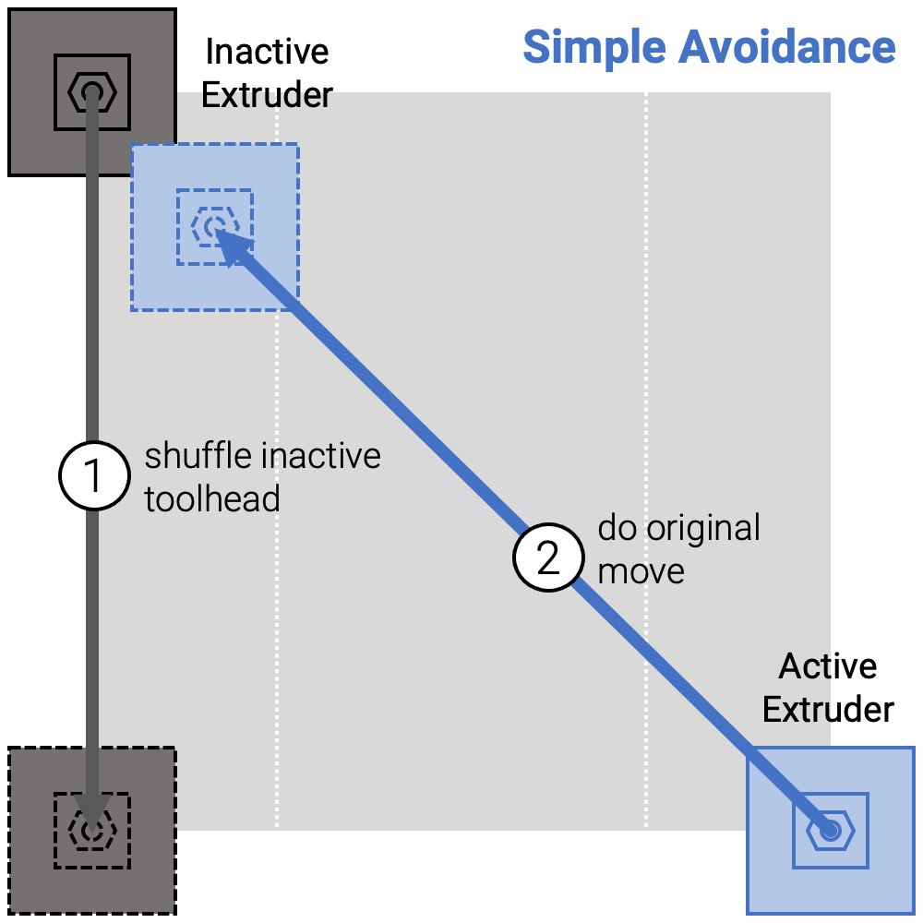
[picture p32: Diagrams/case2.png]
|  | **Case 2: Simple Avoidance**<p><p>If a move enters the endzone and there's a detected collision - more precisely: <p><p>“the bounds of the active toolhead’s travel intersect the inactive toolhead's bounds" <p><p> …then an active intervention, in the form of an **"endzone shuffle"**, is needed.  This will be our term for an inactive toolhead moving from the front to the back, or the back to the front, to get out of the way of the active toolhead.  <p><p>Say the inactive extruder is in the way - in a corner - and is approached via an X move.  The inactive extruder must get out of the way, by doing an endzone shuffle.  To minimize print artifacts, a filament retract is needed here, followed by the original move.  This is the simple avoidance case:<p><p>(1) shuffle inactive toolhead<p><p>(2) do original move.<p><p>Full-length endzone shuffles (corner-to-corner moves) are not required, or optimal, but are simpler to implement and explain.  Assume for the rest of the discussion here that all toolhead parking is in a corner.
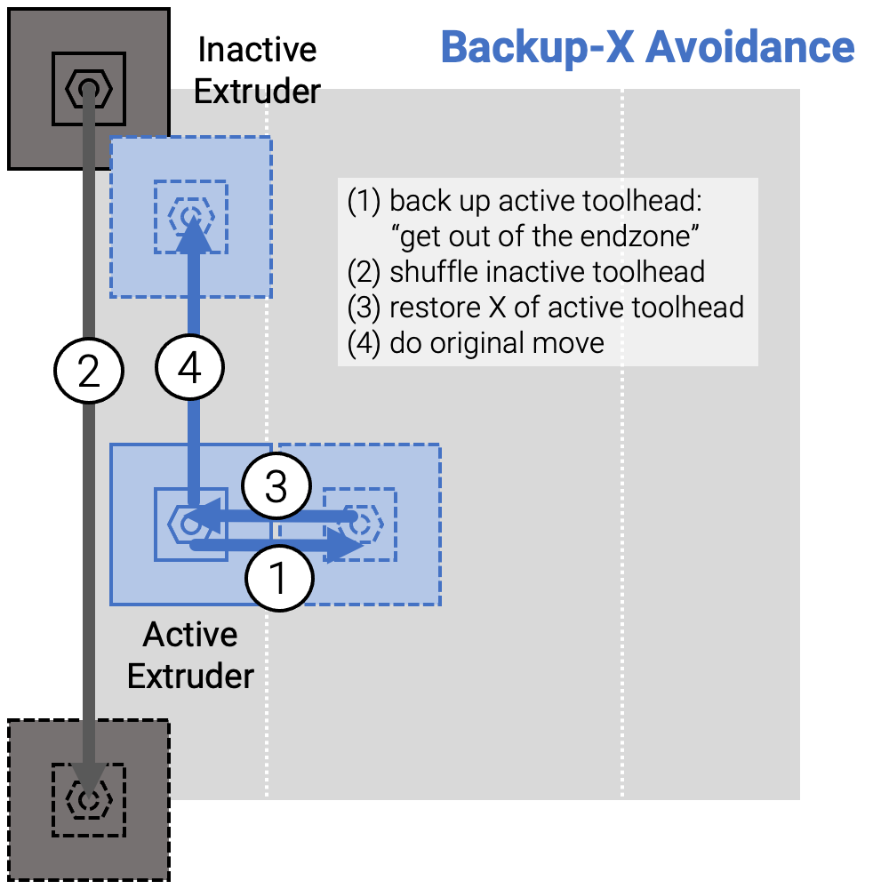
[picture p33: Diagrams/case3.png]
|  | **Case 3: Backup-X Avoidance**<p><p>Now, imagine that the active extruder is in the endzone, in a location where the inactive toolhead would smack into the active extruder during the shuffle, but the active toolhead is not overlapping the final location of the inactive one.<p><p>Here, the answer is to back the active toolhead out of the way first.  The sequence looks like this:<p><p>(1) back up the active toolhead: move it out of the “endzone”<p><p>(2) shuffle inactive toolhead<p><p>(3) restore X position of active toolhead<p><p>(4) do original move<p><p>The picture shows a bit more backup than absolutely needed, but you get the idea. |
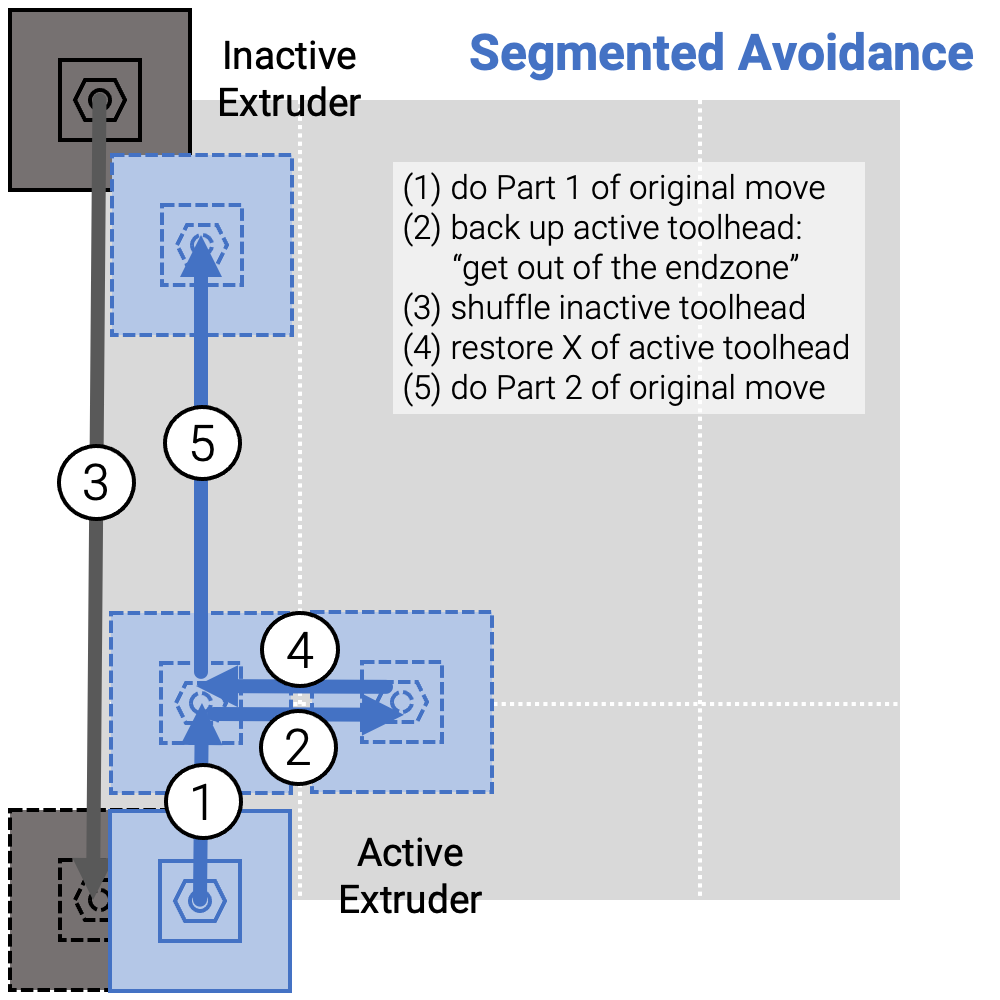
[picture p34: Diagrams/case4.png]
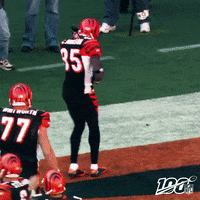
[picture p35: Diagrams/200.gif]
|  | **Case 4: Segmented Avoidance**<p><p>If the inactive toolhead’s shuffle would cause it to overlap with the current active extruder’s position - when it’s in the corner of an endzone - we need to do something a little smarter.<p><p>Say the left toolhead is inactive in the rear left corner, and then the right toolhead continues on a counter-clockwise circle along the edge of the print area, getting to the front left.  The toolheads are now in opposite corners of the same endzone.<p><p>*There is no single move that works.  The two toolheads must switch positions, and the move must be split.*<p><p>Time to do an "**endzone dance**"! <p><p>The move command is split into two parts.  The first part moves the active toolhead into a position where it will no longer interfere with the inactive extruder, post-shuffle. The second part completes the original move from the partway point.  <p><p>The sequence looks like this:<p><p>(1) do first part of the original move<p><p>(2) back up the active toolhead: move it out of the “endzone”<p><p>(3) flip inactive toolhead<p><p>(4) restore X position of active toolhead<p><p>(5) do second part of the original move<p><p>The first part of the move is necessary to ensure that the Y position of the active toolhead “just clears” the future position of the post-shuffle inactive toolhead.

Endzone dancing adds print time and the potential for print artifacts (from retractions), but it’s necessary to use the full travel.  When does it happen?

##### Worst-case for Segmented Avoidance

The worst case for motion is when **every** travel move triggers an endzone dance; for example, this condition occurs when printing an end of a square and when using a square-aligned infill direction (0 degrees or 90 degrees).

TBD: pics of motions matching this description

More generally, endzone dancing is needed for each outer perimeter of a full-size square.

> This is the downside of the Dual Gantry approach. It is what it is.

However, some straightforward techiques can help us avoid it.

###### Rotate Long Parts

Don’t hang out in the endzone if it’s not necessary! Long, skinny parts can be reoriented to use the full Y height with park-in-the-back mode, or on a diagonal with the park-in-opposite-corners mode.

###### Rotate Infill

Rotate the infill direction to 45 degrees, so that the inactive extruder is only in the way twice for each square.

###### Use Fewer Perimeters

Avoid outer perimeters on large parts to avoid endzone dancing.  For example, go from 4 to 3 outer perimeters and increase the outer perimeter width to compensate.

###### Minimal Shuffles

Instead of doing a full-Y-travel move for each flip, what about minimizing the shuffle distance to only what’s necessary?

###### Simultaneous Motion

The inactive extruder could get out of the way, while the extruder is on the other side, to hide some of the time cost of the dancing.  

Simultaneous motion can be triggered with the two-Klipper control option, where each gantry is independently controlled.  Doing this with RepRapFirmware would require at least minor changes to the generated G-code to drive XY and UV (second-gantry) axes simultaneously.  Any implementation that assumes the use of `T0` and `T1` commands to share XY move commands between gantries cannot enable this.

###### Preemptive Positioning

The G-code processor could be smarter with positioning to avoid the need for retractions for interesting shapes, like a C-shaped part where one toolhead preemptively darts to the correct spot to get out of the way, or even just parks in the crook of the C shape and never moves.

### Duplication and Mirroring

A side benefit of Dual Gantry - like IDEX - is the option of simultaneous multi-part modes that split up the workspace.  Here, we assume that collision detection and avoidance enables full workspace access.

* Duplication Mode: like an IDEX, split the workspace in two:
  * Usable bed space: divide the bed in two.
    * 2x 85 x 170.

* Mirror mode: similar, but you leave space for the toolheads to never touch, so less space is usable.
  * Usable bed space: divide the bed in two and leave an interior gutter.
    * 2x 60 x 170.

However, you could get more flexibility to use the space with a slight bit of slicer awareness.  Imagine offsetting the start Y positions for two mirrored parts so that you get effectively higher overlap than a simple static partitioning (two circles, each larger than half the bed width or height).  You could print two half-bed-size triangles at the same time, for example.

Or, imagine having two streams of independent G-code, where the streams are sync’ed at Z moves.  

[Apparently this will be a thing for RRF for version 3.5](https://forum.duet3d.com/topic/29023/independent-dual-gantry-any-examples-out-there/3?_=1656291960523)!

You can then print completely different parts at the same time.  How cool is that?  IDEX can never do that.

### Current Software Implementations

The software and firmware side for Dual Gantry printers will be an evolving space - to implement the optimizations described above, but also to reduce the complexity of configuration and tuning for new builds.

**Watch out for new stuff here.  Join in!**

At minimum, any Dual Gantry-capable firmware needs to control both gantries.  If you want full travel, you also need *something* to ensure safety and insert moves with added G-codes.  

You’ll need to align the toolheads in XYZ too.  Z alignment can be easily automated with a shared Tri-Zero nozzle endstop. XY alignment is the same process as with an IDEX, of either:
* measuring with Vernier-style or other test prints or macros
* jogging printer motion with an upward-facing nozzle camera to measure the temp offset
* connecting up to a camera and using machine vision a la [TAMV](https://jubilee3d.com/index.php?title=TAMV)

Below are your software options.. at least, the ones that come from Zruncho with :heart:.

#### RepRapFirmware (RRF)

RRF has built-in support for CoreXYUV built-in, which makes it stupid simple here to at least get the axes in motion.  You select this printer type with a single G-code command, where you map the X, Y, U, and V axes to your printer control board’s stepper outputs.  Then you configure a homing macro to home all axes, and then you add macros to execute on each toolchange, specifically, to park the toolheads in opposing corners.

As long as the slicer spits out `T0` and `T1` commands, like for an IDEX, everything should then “just work”, for the `Dual Toolhead, No Avoidance Needed` case.

This was a big surprise!  

In fact, the main Duet/RRF developer, David Crocker, made it easy and general for all kinds of “linear axis combination” machines to flexibly use the same firmware.   See [this forum post](https://forum.duet3d.com/topic/22850/stacked-dual-markforged-kinematics-possible?_=1655971338993):

> "...after I implemented CoreXY, CoreXZ, Core XYU and CoreXYUV kinematics, I got fed up with having to add a new kinematics class every time someone wanted another variant of CoreXY. That is why RRF now has a universal linear kinematics class, which supports any kinematics for which the motion of every axis is a linear combination of the motion of each axis motor, up to the maximum number of axes supported."

That’s what we have here - a 2 simple linear combinations for motion.

Nice going, David!  Impressive foresight.

RRF “just works” here.  There is a known-good configuration for a Duet 2 Wifi board in the `Configs/Duet2RRF` folder.   

NOTE: This config is gantry-only. You’ll need to add your Z and E config.

For the curious, here are the most relevant RepRapFirmware documentation pages:

* [Configuring RepRapFirmware for CoreXY Printer](https://docs.duet3d.com/en/User_manual/Machine_configuration/Configuration_coreXY)
* [M669]((https://docs.duet3d.com/User_manual/Reference/Gcodes#m669-set-kinematics-type-and-kinematics-parameters)): Set type to K8 (CoreXYUV)
* [M584](https://docs.duet3d.com/User_manual/Reference/Gcodes#m584-set-drive-mapping): Set drive mapping (add U & V axes)
* [M563](https://docs.duet3d.com/User_manual/Reference/Gcodes#m563-define-or-remove-a-tool): Define tools

**To be clear, this config does not handle the `Dual Toolhead, With Avoidance Needed` case.**

To support that case, you would need to make at least these changes:

* Change printer config type to not map XY and UV axes to XY motion commands: in the M669 command, change away from type K8, probably to K1 and with a custom movement matrix
* Generate separate XY and UV commands in the G-code post-processor
* Replace `T0` and `T1` macros with G-code equivalents

#### Klipper

Klipper supports a massive ecosystem of control boards, sees new features added frequently (especially Input Shaper), and supports many toolhead boards that work well in a printer with tiny toolheads like Dueling Zero.

##### Klipper Kinematics Patch for Dual Gantry CoreXY

As of 2023-07-03, Klipper mainline code does not *directly* support a Dual Gantry printer.   Which is fine... Kevin (the main Klipper dev) has a high bar for Klipper additions - ideally having value to many people - and there aren't many Dueling Zeros.  

No problem, though.  Thanks to a collaboration between Zruncho and Tircown (a developer of the highly-related Klipper IDEX code), code is avialable here:

* [GitHub Klipper fork with Dual Gantry additions](https://github.com/zruncho3d/klipper/tree/dual_gantry_main)

You'll have to change your local Klipper code to use the dual_gantry_main branch, plus you'll have to restart Klipper so that the new code takes effect.  

Since the changes live entirely within a single file (`klippy/kinematics/dualgantry_corexy.py`), there's a good chance that if you rebase this code to the latest Klipper, it will "just work". There's a chicken-and-egg situtation here toward a mainline release that can only be resolved when enough people have these, share them, and show the code running.  Then it justifies a merge, and it's even easier for the next people to get them.

**NOTE**: If you do not rebase onto the latest Klipper code, you'll be missing out on recent bugfixes and feature additions, plus, your existing toolhead and driver boards may not connect if they have been previously flashed with a more recent version.  You definitely want to rebase this branch onto whatever is the latest code.

**NOTE: HERE BE DRAGONS**.  There's a lot of config that is not yet documented here.  If you get stuck, ask on the ``#dueling-zero-dev` on the ``#tri-zero` channel on the DoomCube Discord.  But this can be fun, too.

The docs are currently just about the bare minimum; they certainly will get more prescriptive and complete over time, especially if you share your build on the Voron Forum or ``#dueling-zero-dev` thread on the `#tri-zero` channel on the DoomCube Discord.  

For example, if you're reading this... you should get your entire printer working first without the custom branch, with a successful single-extruder print.  THEN proceed to make the two work together.

**Configuration:**

To use Dual Gantry support from the branch above, the minimal Klipper configuration must:
* Add [stepper_u] and [stepper_v] sections for the second gantry, along with corresponding stepper-driver sections
* Specify `kinematics: dualgantry_corexy` in the printer section
* Define T0 and T1 macros with SET_DUAL_CARRIAGE inside

You'll have to modify an existing sample config.

However, all kinds of other stuff must evolve when going from one to two extruders.  `PRINT_START`, `CANCEL`, even `HOME`, are all are macros that really need dual-extruder awareness to prevent collisions in all cases.  Take a look at these.

#### Software Smart Avoidance

This repo includes a G-code processing code called duel.py that receives a G-Code file to safely handle all movement cases.  It has to assume a starting position and needs the specific toolhead-size and XY motion bounds.  

`duel.py` uses a few Python modules to simplify the implementation:
* [gcodeparser](https://pypi.org/project/gcodeparser/): a simple parser to turn ASCII lines into modifiable python objects
* [requests](https://pypi.org/project/requests/): the usual Pythonic way to do clean REST interactions
* [cmd](https://docs.python.org/3/library/cmd.html): a simple way in Python to do interactive programs.  “Battle mode” is a little easter egg.
* [shapely](https://pypi.org/project/Shapely/): a geometry library
* [nose](https://pypi.org/project/nose/): test-running library

The polygon intersect from Shapely enables interference detection.

That code looks like this, with a function `get_toolhead_bounds()` to get toolhead bounds as a shapely.geometry.Polygon instance:

```
    poly1 = get_toolhead_bounds(p1)
    poly2 = get_toolhead_bounds(p2)
    overlap = poly1.intersects(poly2)
```

One mildly interesting bit is the move split needed for the Segmented Avoidance case, which can be handled with basic y = mx + b math.  

Aside from these bits, the code is pretty straightforward... surprisingly so.

`duel.py` is also capable of driving two independent Klipper instances in a "Ships in the Night"-style setup.  This code enabled me to validate the avoidance algorithms on a real printer, before modifying Klipper, but for all kinds of reasons, the integrated Klipper version is better: no static port partitioning, no easy ability to use a shared nozzle endstop, and no ability to use a single web interface for the whole printer, amongst other issues.

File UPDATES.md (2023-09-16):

### 2023-07-03: a little update: interest is growing!
In mid-2023 the interest has been picking up, as more people learn about the printer.  Community development includes [Desune's Dueling Boops variant](https://github.com/desune2487/Dueling_Boops), Chadonka's gantry board mounts, and more stuff that should be released shortly.

Zruncho's back on it, too.  Tri-Zero spinoffs, like [ZeroPanels v3](https://www.youtube.com/watch?v=6F5wUP4zZDg), have been tested first on Dueling Zero.  Watch this space carefully for major updates to documentation and design...

Also: Klipper code is more easily found [here](https://github.com/zruncho3d/klipper/tree/dual_gantry_main) now, as well as on the SOFTWARE page here.

### 2022-08-20: Alpha-1  
This first release covers everything you need to build and run your own Dueling Zero: CAD, STLs, DXFs, sample firmware configs, smart avoidance code, G-code streaming code, instructions, and a parts list... everything but an illustrated manual.  But if you're reading this, you almost certainly don't need a manual, anyway.

To make it easy for anyone to grok this crazy Dual Gantry layout - and learn about its opportunities and challenges, both in hardware and software - the repo walks through the software and the design.

**NOTE:**
See the [Archived_v1](Archived_v1) for this original content.

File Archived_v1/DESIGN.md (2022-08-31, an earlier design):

## Design Walkthrough

Whenever I see an interesting new printer, or even a non-trivial mod, I don't want to just get access to the STLs or CAD...

I want to know what the designer was thinking, and why.  

I want to learn from them, to understand the design, as well as how it can be improved.

I want to avoid wasting time going down dead-ends trying to make it better, especially ones the designer has already gone down.

Dueling Zero will probably evolve faster with more eyes and more CAD designers taking a crack at it.  So to encourage action there, this section provides a walkthrough of the current status of the Dueling Zero design, covering all the key parts that are unique to it.  At the end are bonus pics from the early prototypes.

**The #1 thing about the design: it's all about being pragmatic**.

D0 is heavily optimized for using off-the-shelf parts from the stock V0 parts catalog, with off-the-shelf geometry... vs optimized for motion travel, or cost, or anything else.

Put another way, optimized for time-to-market.

**It’s not squeezing out every mm, and should have plenty of opportunities for travel optimization later.**

With that small caveat out of the way... I think there’s a lot of interesting stuff here!

More changes were needed than originally expected, and this section tries to summarize those changed or completely new parts.  Surprisingly, the toolheads and almost all Z parts are unmodified.

Highlights:

* No fundamentally new non-printed parts are needed.  You don’t need to cut any extrusions, and few holes need to be drilled.
* The entire gantry floats within the frame.  After building, you can loosen 12 screws and then slide it up or down to balance umbilical rubbing against Z travel.
* Correct, *there are no Z rails*.  This is not a CAD mistake.  I didn’t feel like buying any, and I didn’t know the optimal size anyway.  Printed sliders work fine as a replacement for rails, and you should expect more info about them soon.  If you want proper Z rails, no problem! They'll fit in place, just like on a regular T0.

### XY Motion

The soul of *this* new machine.  A two-headed beast.

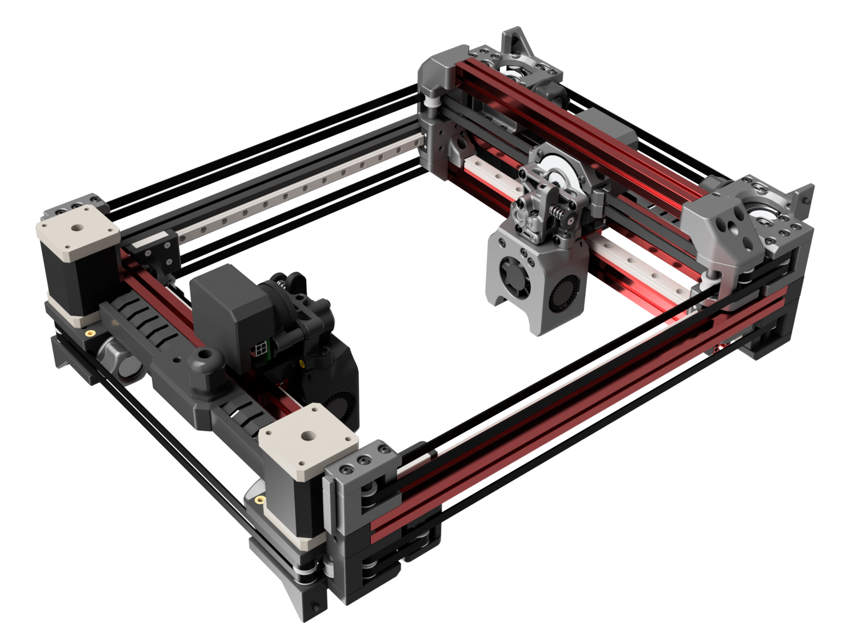
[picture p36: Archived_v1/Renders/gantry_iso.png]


The low-side (black, left-side) gantry went first, as I really wanted to improve the belt-mounting path on the carriage first, and *then* modify the resulting carriage design to support a higher set of belt mounts.

#### Low-side gantry

Take a look.  It's now underslung:

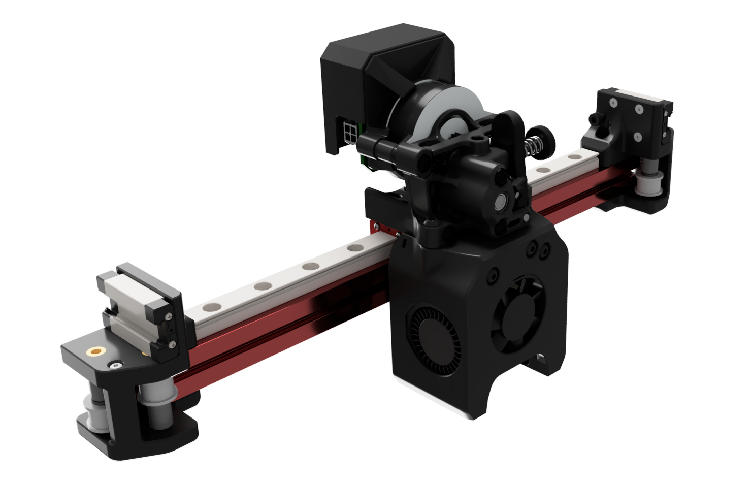
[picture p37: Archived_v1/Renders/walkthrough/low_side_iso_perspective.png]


##### New Short X Carriage

The new X carriage is based on Double Dragon X carriage geometry, but modified to support both belts in one carriage.

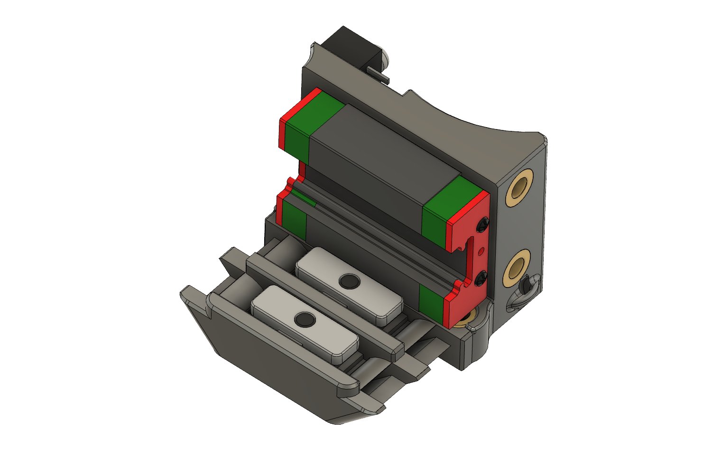
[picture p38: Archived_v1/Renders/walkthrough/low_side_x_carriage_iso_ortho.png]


This new X carriage improves on the stock V0 carriage by enabling the belt loops to come back on the sides, providing grip for future re-belting, especially for printers where you can’t loosen the front idlers.

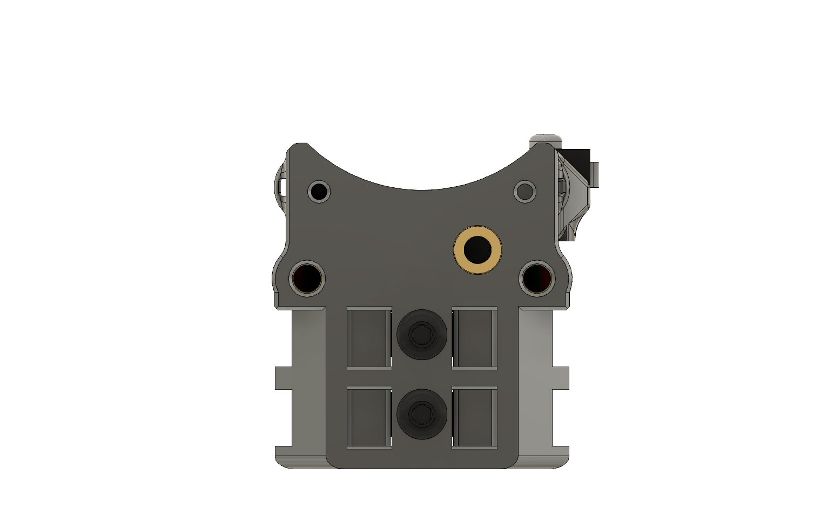
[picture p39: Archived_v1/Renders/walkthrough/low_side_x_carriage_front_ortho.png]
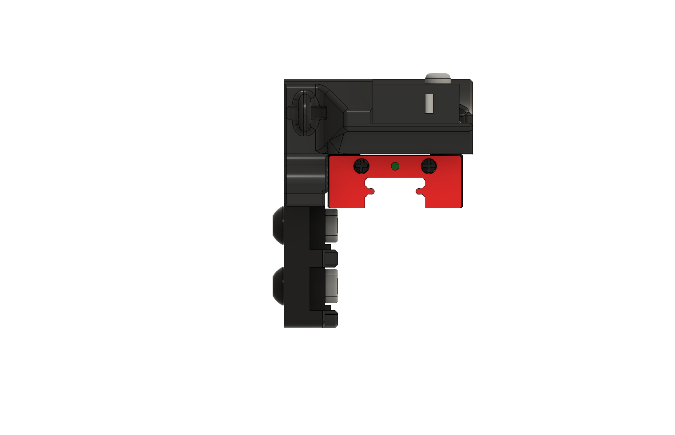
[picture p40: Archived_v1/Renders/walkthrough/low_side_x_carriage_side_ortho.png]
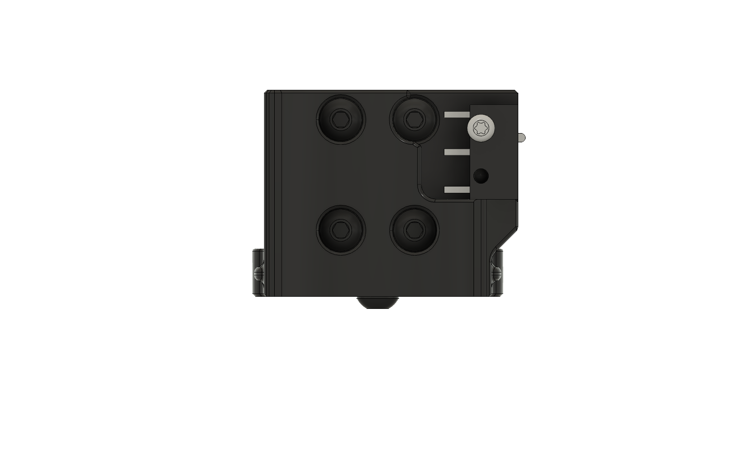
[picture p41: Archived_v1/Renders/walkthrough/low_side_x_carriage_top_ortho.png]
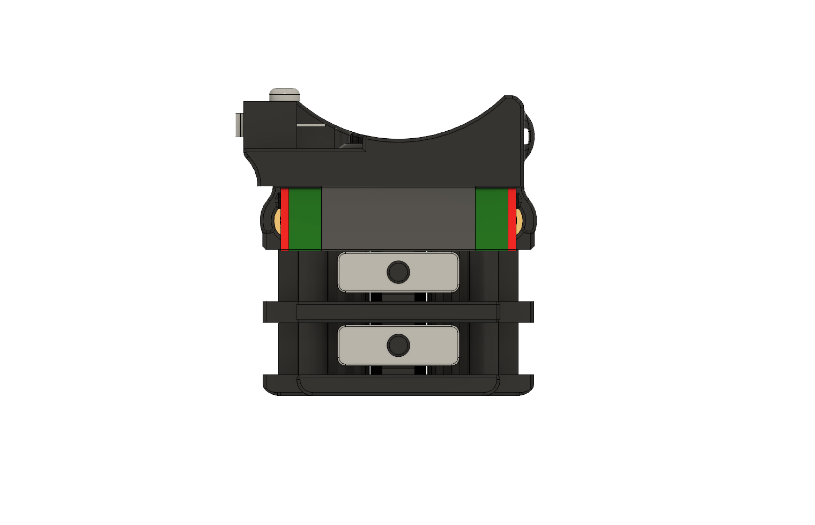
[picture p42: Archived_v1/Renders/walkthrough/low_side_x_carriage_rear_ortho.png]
|  |  |  |  |
| - | - | - | - |

Highly recommended for your regular V0 or V0 mod!  Having to clip belts to length sucks.  No more, with this part.  You can see the belt path from the section view below.

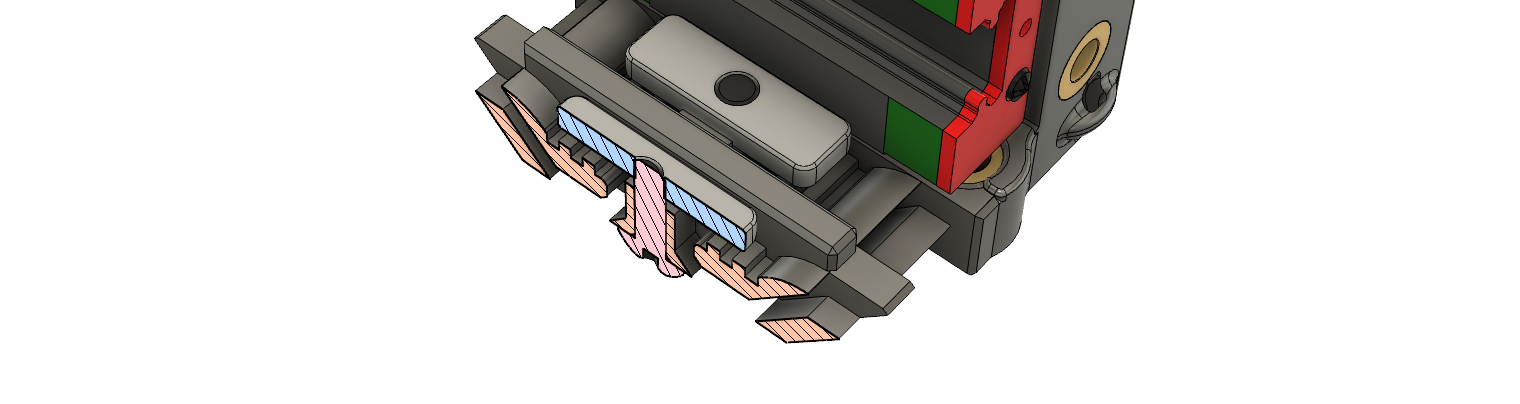
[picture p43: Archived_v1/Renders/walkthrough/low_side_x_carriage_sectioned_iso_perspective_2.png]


Note also: this part is MGN9C-only.  MGN9C is a great mod to reduce the potential for "toolhead flop".  With the default low-preload MGN7 rails, especially when combined with a plastic carriage, there is a possibility of unwanted toolhead motion.  MGN9C adds a little weight and size, but you can trust the rigidity more.

##### Low-side XY Joints

These are a flipped-upside-down version of the original V0.1 XY joints:

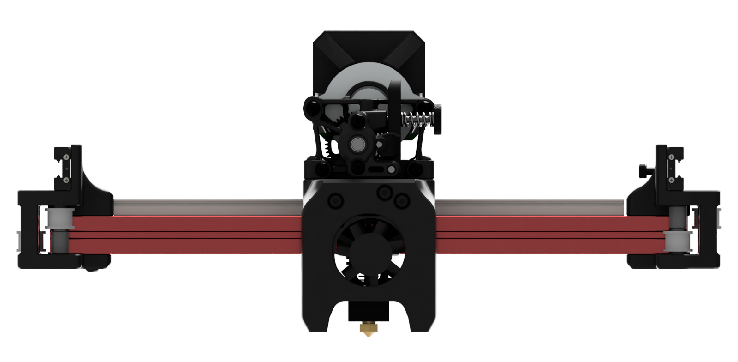
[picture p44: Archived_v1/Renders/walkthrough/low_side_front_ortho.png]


The flipped orientation enables both gantries to share the same pair of rails.  A few counterbores had to be reversed and the height for extrusion mounting needed a lil' adjustment, but that was it.

|  |  |  |
| - | - | - |

The endstop mounting on one side is simple and adjustable.  It's a hole for a screw to form a thread.  The edge of a SHCS hits the plunger on a microswitch, directly.



#### High-side (high) gantry

This is the much more interesting half, with some new stuff:



The challenge here is that when you flip the belts to live above the carriages, the belts want to go through the extruder motor.  So you have to find a way to terminate the belt connections in a tight space, at a location that is away from the original crossbar, and hence, subject to large forces from the belt tension.

|  |  |  |
| - | - | - |

Reminds me a bit of the [Narushevich](https://www.airplane-pictures.net/manufacturer.php?p=1458)!

The toolhead looks like this, and has some real advantages.

|  |  | 
| - | - | - |

For example:
* You can remove the Sherpa Mini extruder while leaving the toolhead board, carriage mount, and cowling in place.  Extruder maintenance is super-easy: remove two screws and one plug.
* The toolhead board mount is much more rigid, which should provide more faithful Input Shaper measurements for toolheads with integrated ADXLs (like Huvud 0.61, FLY-SHT42, or EBB42).
* The MiniAS supports a wide variety of hotends, and even multiple extruders.  It's a nice design.
* You can easily change out the entire X carriage assembly and retain the original tensioning setting.

However, the design is currently specific to the motor positioning of the MiniAS and the Sherpa Mini.  You can't currently use a MiniAB, as the holes there would be much lower, because the motor mounts lower.   

##### New Tall X Carriage

You've probably never seen a carriage mount quite like this. It’s a mod of the low-side X carriage, with provisions for belt attachments as well as a more rigid toolhead board mount.

|  |  |  |
| - | - | - |

The lower belt attachments remain, so that you can use the same part on the low side too, with the benefit of the more rigid toolhead board mount.  This isn't shown in the renders yet, but it's not too hard to imagine.

##### Belt Grabs

The geometry of the belt attachments comes from F-Zero and Tri-Zero, which use toolless belt grabs for their Z axes.  



This geometry works great here too, and it makes the entire toolhead easy to remove and then add back.  That’s important for a designer expecting to make many X carriage tweaks, for example, to add wire management, but probably not a big benfits for most builders.  

##### Toolhead Board Mount

The toolhead mount is sized for a NEMA17-hole-pattern-compatible square toolhead board.



For now, this part assumes board-specific spacers to work with multiple board-spacer heights, but it could (and probably should) be an integrated part in the future with board-height-specific variants.

##### Y Toolhead Strut

This part strengthens and locks in all the belt grabs, but also provides a surface to rigidly mount the toolhead plate on top.



The whole X assembly here is so much more rigid than in Double Dragon, where the entire toolhead board and shroud is dangling and can flex behind the extruder stepper.

##### Y Gantry Strut

Why?  Without this, the belt tensioning forces bend the upper XY joints inwards, which would surely cause belt damage over time.  Resist the forces!



Going with a strut was the fastest design solution here.  I don't particularly like it.  It gets in the way of tightening things.

In a future design, a symmetric gantry with changed motor and cowling mounts might remove the need for this part entirely.  

##### High-side XY joints

These ended up as a 4-part stack.  The geometry complexity enables support-free printability.



It's not the most elegant, but it works.  And it's rigid enough to transfer belt tensioning forces to the strut.

|  |  |  |
| - | - | - |

#### X Endstops

The new height of the gantry crossbar relative to the AB blocks meant that the endstop had to move.  Here, it’s a minimal, adjustable, and symmetric design.



A similar matching part holds the microswitch to the gantry crossbar.  



NOTE: on D0 these are X endstops.  On a V0 or similar, these would be Y endstops.  It's all twisted!

#### Modified BoxZero AB blocks

To get closer to full X motion, BoxZero idlers needed a mod to provide more clearance for a "toolhead backpack" - the area behind the motor where a toolhead board can go.  Normally such a cutout wouldn’t be needed, but the changed height of the fixed gantry-frame crossbar causes the toolhead-board backpack to get in the way.



This notched version is only needed on the high-side gantry, so if converting from a regular B0, you can reuse the AB blocks.

#### BoxZero-derived idlers



These parts are not strictly needed, and in fact, originally the gantry used stock B0 idlers, but they provide visual symmetry with the AB blocks (I know, I know...).



These use the usual V0 9mm drive spacers.

#### Toolhead Umbilical Receiver

Derived, in principle, from the F0 umbilical, but without a cover.  Fits a cable gland and routes wires to the nearby cable channels.



A potential improvement here: to add push-fit connections on top and bottom, to enable low-friction rotation of the reverse bowden tube, as well as enable variable-length reverse bowden tubes to the filament feed.

### Z Motion

#### Z Sliders

Oh yes.  They’re real, and they’re spectacular :smile:.  

## [>>> See YouTube video of sliding motion!](https://youtu.be/JXZt2rP1yQQ)

|  |  |  |
| - | - | - |

They're extremely simple and low-cost. Each uses the geometry from a ZeroPanels panel, extruded, with 4 holes added to match a typical MGN7H carraige.

They're flexible.  Literally... the flex makes it possible to insert and remove them without taking a rail apart.

The key to making them properly is to use the edge of an extrusion as a planer to gently remove a tiny amount of plastic, so that the printed slider fits tightly in place, without backlash or excessive friction. You can get the technique pretty easily, and if you screw up, just throw it away and start again.  Remove move material equally from both ends of one side, gentry, until you notice the grip lessen as you slide the slider in the exact extrusion you'll be using.  Yes, matching each slider to the extrusion helps.  There is surprising variance not just between extrusion brands, but also batches, and even between slots on the same extrusion piece.  You can probably also modify the geomtry slightly to get really close without the planer action.

These work fine without lube, but with a little Super Lube, they’re comparably smooth to actual rails.  Don’t expect them to handle large side or twisting loads, but for the highly constrained loads they have (up and down Z), they seem just fine, especially with the front bedframe and rear Z designs here that support tensioning.

In the future, these can be easily changed to *not* stick out the sides, to enable the use of flush-fitting default V0 side panels.

#### Front Idler Mounts

This is a surprisingly interesting part.

From the front view, you see a boring old box.  



Soooo boring, right?  But this part hides a secret entrance.

You need space for a screw head to go in, but a straight screw would conflict with the tensioning screw and heatset used with T0.  Sure, you could make this part and the corresponding Z idler wider... unlike T0, the space is available; there's a huge gap from these parts to gantry with the superwide layout.  But  that's lazy talk.  I wanted to keep the parts as stock as possible here, to reduce the time cost of conversions.

The solution: add an oblique-angled access hole for a balldriver to tighten the main screw, combined with a slot to insert that screw without requiring disassembly.



You can see the slot above, peeking through the oblique access hole.

|  |  |  |
| - | - | - |

After all - once you've built the double-gantry unit, you really don't want to take it apart again.   You can’t see the angled hole for screw access, or the area where the part slides in!  Just looks like a box from the outside.

#### Unmodified T0 Rear Z Motor Mount

This one was a happy little accident.



The T0 rear Z motor mount part did not need to be modified.  The motor is flipped from its usual orientation, with simple spacers added so the belt can escape through.

One part that didn't demand a redesign.... I'll take it.

#### Rear Z "Crossbar Corners"

These take geometry cues from the BoxZero corners:



They enable a mount for the modified ZeroClick dock, as well as the rear Z parts.

Since no blind joints are used here, this part can slide up and down at will...

#### Unmodified T0 Rear Z Idler Base

... which helps set the rear Z height.  Z can be adjusted after the frame has been built.



This whole area is unmodified T0 stuff, currently.

It's absolutely a place where there's tons of opportunity to get back Z, possibly even without parts changes, just by raising the rear Z crossbar and adjusting the Zeroclick dock to match.

It's also a design that isn't truly locked-in, to properly resist Z tensioning forces.  Extending the rear Z idler base to lock against the rear Z crossbar would solve this potential issue, easily.

#### Larger bedframe, with new Wago mounts

This is more of a T0+ thing, but it's worth calling out, until T0+ is separately released and documented.



A few small mods were needed:
* Widened-by-15mm T0 Bedframe Z Mounts
* Fromt bed mounts adjusted to fit the 180x180 bed.





The widened front-corner Z mounts have a side hole added to enable preload adjustment.  Haven't tried these out yet, but they should help with fine-tuning the Z motion, and possibly increasing the friction, intentionally, to increase the bed hold.

### Frame

#### Modified BoxZero Corners

BoxZero corners provide a nice bump in rigidity for 1515 frames.  Instead of a 7.5mm offset with a single screw, most corners have two screws and a 37.5mm offset.

Since the default D0 size is wider, taller, and deeper, it make sense to add 4 more BoxZero corners to the bottom of the frame for even more rigidity.  Since the optimal size seemed close to 330mm, adding 15mm to each end seemed logical, to enable off-the-shelf 300mm extrusion packs.

Here are the 3 new variants, each of which has a mirrored version too:

|  |  |  |
| - | - | - |

The bottom rear corners provide a large opening for cables, so that 2 stepper cables, an endstop cable, and a full toolhead cable can pass through the frame without issue.

#### Modified ZeroClick Dock

ZeroClick handles probing here.



The usual ZeroClick Side Dock needed a few mods to fit here: changes to depth, height, and even a shave off the top.

#### Cable Channels

These derive from ones first made available with Double Dragon:

|  |  |
| - | - |

There's one on each side of the umbilical receiver to hold and hide the stepper and toolhead cables.

### Other Mods

Even more mods... these were all straightforward:
* 25mm T0 Side Skirts added for the longer depth
* 65mm T0 Front Skirts added for the custom width

### Prototypes

If you have V0 AB blocks lying around, you can even make a test gantry like this:

|  |  |
| - | - |

This was the first test gantry to prove out the concept.  BoxZero AB blocks are a much better fit, though, as they enable you to build the gantry separately, then drop it into the frame from the top.  

The second test gantry moved to BoxZero-derived ABs, with additional width and length, and lived for a bit in a "stubby Z" test config.  This one had an unpowered Z travel of 10mm (!), but it helped with iterating on gantry and bed parts.  In particular, the test gantry made clear that achieving a target X motion of 170mm would require adding width.

|  |  |  |
| - | - | - |

The third and final gantry is 30mm wider, using 15mm corner cubes between 300mm horizontal extrusions and the frame.  Once belted up, this gantry supported validation of the collision avoidance code.  Let’s just say the toolheads have butted heads once or twice!

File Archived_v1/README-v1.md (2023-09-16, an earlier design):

The v1 gantry refers to original release from August 2022, with asymmetric underslung gantries: a low side, plus a high side with a strut.

There's nothing _wrong_ with this gantry, and Zruncho got 300 hrs out of his before upgrading, but it has some drawbacks relative to the v3:
* more unique parts
* less travel available in XY
* no nozzle-based bed probing
* top-mount rails constrain toolhead availability, somewhat
* different weights for each moving gantry means different input shaper values

All the v1 content is left here, to make things easier to find for those with builds in progress, or for those curious about the (more complex) design process with this one.

**See the [Design](DESIGN.md) page** - this has a visual walkthrough of every interesting part.





Reality:

|  |  |  |
| - | - | - |

Renders:

|  |  |  |
| - | - | - |

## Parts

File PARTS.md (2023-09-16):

## Parts List

In general, none of the parts here should be a surprise.  Beyond anything D0-specific, you'll need everything to build at least one V0, likely a Tri-Zero, but also everything for the Boops and extra toolhead.

#### Rails

| Part | Qty | Qty | Notes |
| - | - | - | - |
| X rails | [300mm MGN7H](https://www.aliexpress.com/item/2251832694486732.html?) | 2x | Make sure to also buy a ‘Carriage Only’ part and message the seller to add it to the rail before they ship it. |
| Y rails | [250mm MGN9H rails](https://www.aliexpress.com/item/2251832586981749.htm) | 2x | Make sure to order high (Z1) preload |
| Z rails | 200mm-220mm MGN7H | 4x | |

#### Extrusions

NOTE: the CAD is not the right size.  It's Zruncho's build size.  Which doesn't quite get you a full 180 cube.

The recommended frame size enables a full 180x180x180 build volume, with a bit of extra travel in the rear Y area for a nozzle endstop, nozzle brush, and maybe a camera for alignment.  Yes, you can build a smaller test bed build, but the travel won't be practical.

You can start from a V0 kit and end-join (BoxZero-style) the chunks ([process described here](https://github.com/zruncho3d/BoxZero#assembly-notes)), as well as use 1515 supplements cut to length to get a choice of color.  If the size is close for the verticals, you can bridge the gap slightly with BoxZero corners (e.g., 400 + 50 -> 450 with B0 corners).

For build areas beyond 180x180 in XY, frame stability becomes a question, and girthier-than-1515 extrusions may be needed - or at least, some form of frame bracing.

1515 extrusions:

| Part | Qty | Dimensions | Notes |
| - | - | - | - |
| frame/gantry/bedframe/rear-brace x-dir | 8 | 350mm |
| frame Y-dir | 4 | 260mm |
| frame Z-dir | 4 | 450mm |
| gantry fixed small Y-dir | 2 | 160mm |
| bedframe Y-dir | 1 | 160mm |
| gantry moving Y-dir | 2 | 250mm |

These parts should yield travel of approximately 188 x 194 x 180 in XYZ.

#### Panels

The bottom baseplate has a complex shape, but all other panels are simple rectangles.

The way to think about the sizes is like this:
* **the baseplate** fits within extrusions, so its size is the inner extrusion size + 4.5mm to fill each extrusion slot - so, inner size + 9mm in total.
* **the exterior panels** fit on top of the extrusions; foam tape and the panels need to cover the 6mm gap to where ZeroPanels plastic fills the extrusion slot, on both sides.  So: inner size + 12mm.

If your panel supplier or extrusion supplier can't guarantee tight tolerances, you may want to drop each size by 1mm to ensure clearance.

| Part | Qty | Dimensions | Material |
| - | - | - | - |
| Baseplate | 1x | 359 mm x 269 mm (with cutouts - TBA to repo!) | 3mm ABS or ACM |
| Front/Back | 2x | 362 mm x 432 mm | 3mm Acrylic in front; acrylic or ABS/ACM in back |
| Sides | 2x | 282 mm x 443 mm | 3mm Acrylic |
| Top | 1x | 362 mm x 282 mm | 3mm Acrylic |

#### Triple-Z vs Single-Z

You can actually do a single-Z-motor build if you want, and then the whole shebang can use 7 drivers and a single board.  This option isn’t shown in CAD, but should work with stock V0 parts, or maybe minor changes.

If you’re not a fan of cantilevers (Zruncho's hand just raised, too...), and you want a more scalable printer (especially to the T0+50mm size), Tri-Zero is a good option, at the small cost of adding 2 extra Z stepper drivers, motors, and a few other motions parts.  It also has a nozzle endstop by default, which enables automatic, or at least measurement-supported, Z offset calibration.  This alone is a reason to use Tri-Zero, given the importance of the first layer in 3D printing.

#### Control Boards

The control board situation is up to you.  In theory, any boards should be fine, as long as you get enough steppers.  

Gantry boards (GBB15) are highly recommended, as they enable a single cable per side, as well as easier toolhead-cable plug/unplug.

Toolhead boards are highly recommended, as they simplify your wiring; CAN and USB enable a much smaller main control board, too.

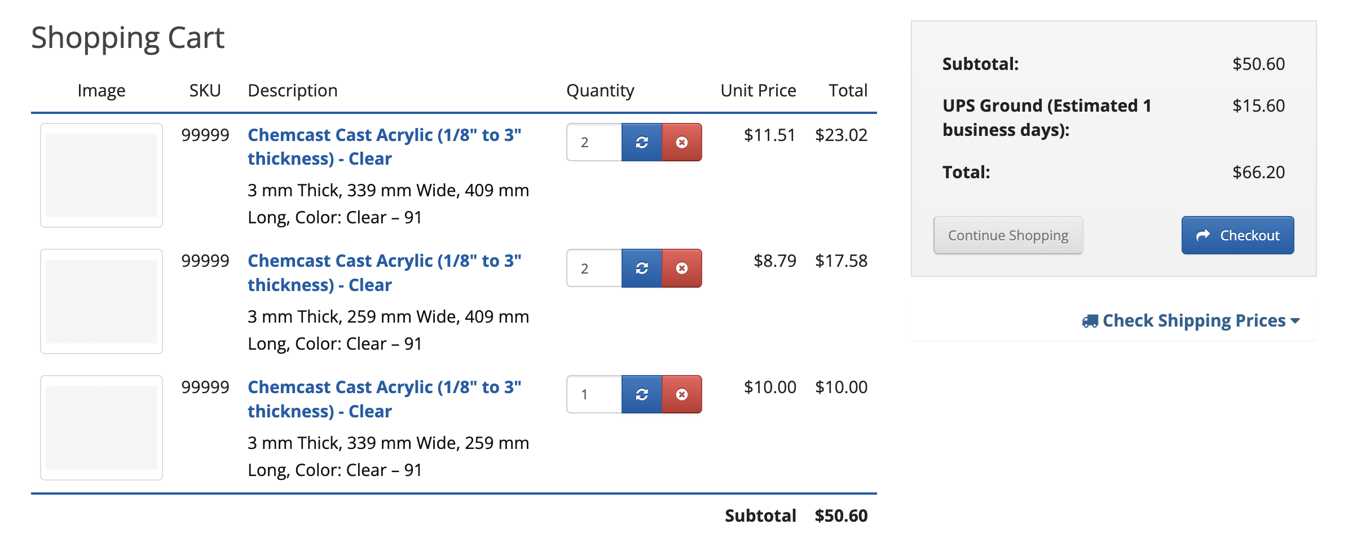
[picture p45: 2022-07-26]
Images/orders/tap_order.png

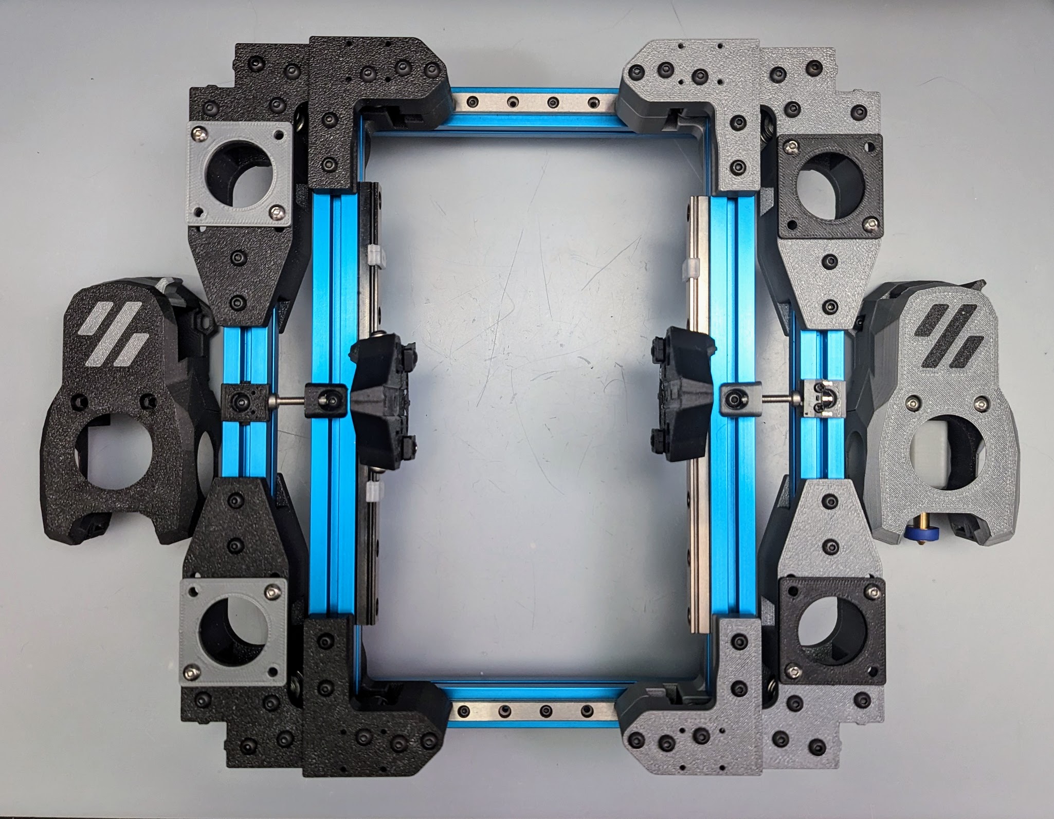
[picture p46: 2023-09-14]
Images/v3/test_gantry_parts.jpg

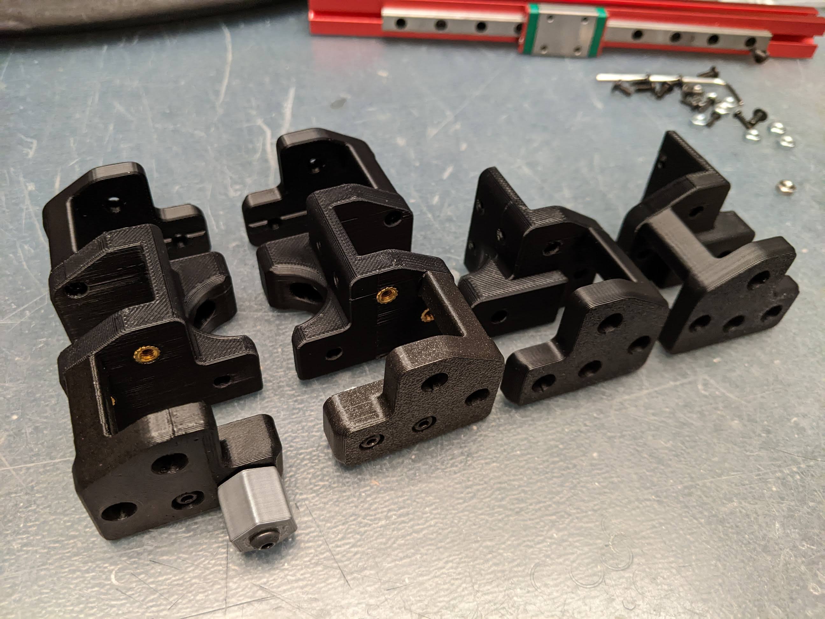
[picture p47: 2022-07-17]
Images/test_gantry/first_carriage_parts.jpg

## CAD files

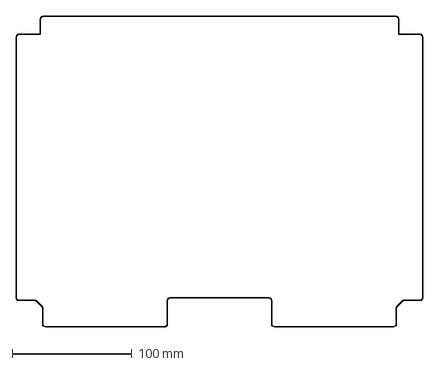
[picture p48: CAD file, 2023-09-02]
DXFs/baseplate.dxf
339.0 x 259.0 mm

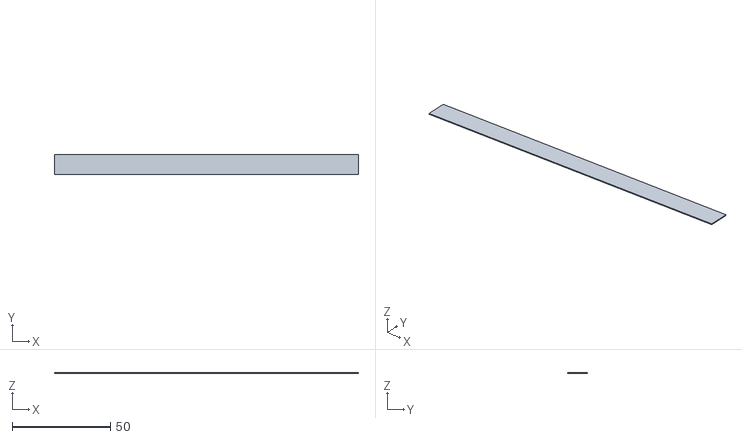
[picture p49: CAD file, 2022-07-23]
src/stl/wide_bar_x.stl
155.0 x 10.0 x 0.4

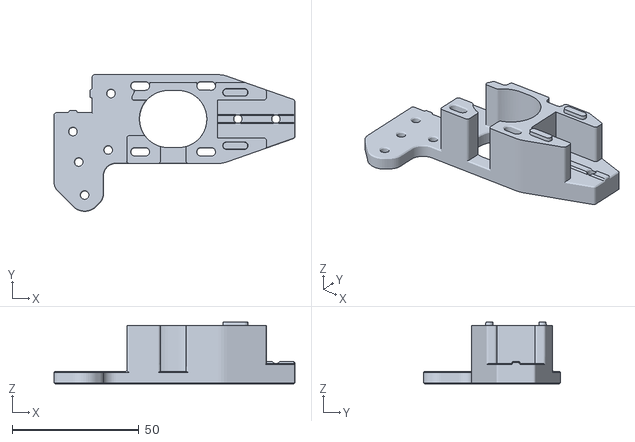
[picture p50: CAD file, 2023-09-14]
STLs/AB_Right_Upper_x2.stl
95.0 x 53.9 x 24.4

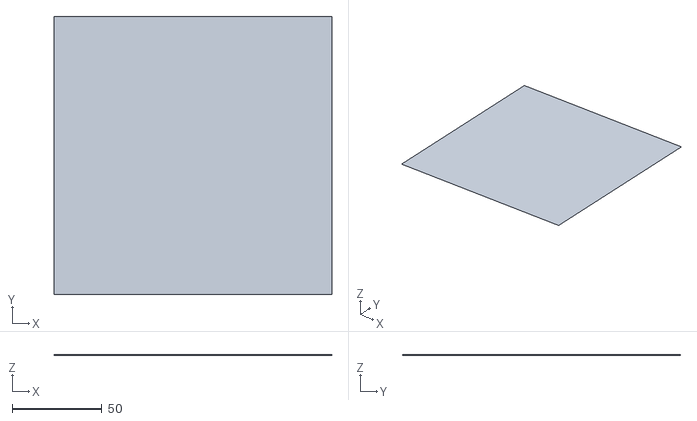
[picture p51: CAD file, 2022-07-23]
src/stl/square_2_layer.stl
155.0 x 155.0 x 0.4

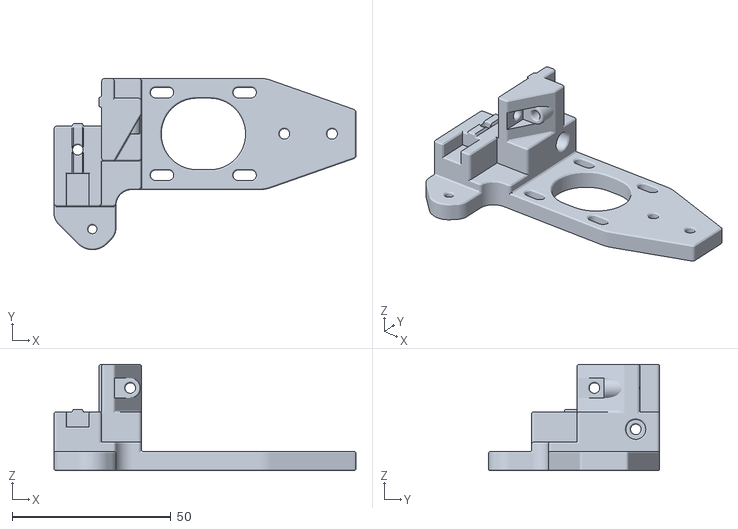
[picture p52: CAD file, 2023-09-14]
STLs/AB_Right_Lower_x2.stl
95.0 x 53.9 x 33.5

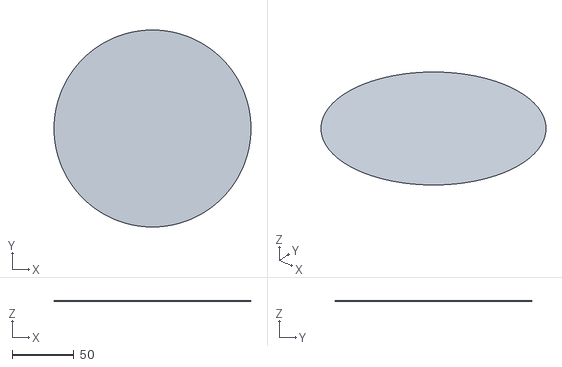
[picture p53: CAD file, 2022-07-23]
src/stl/cylinder_2_layer.stl
160.0 x 160.0 x 0.4

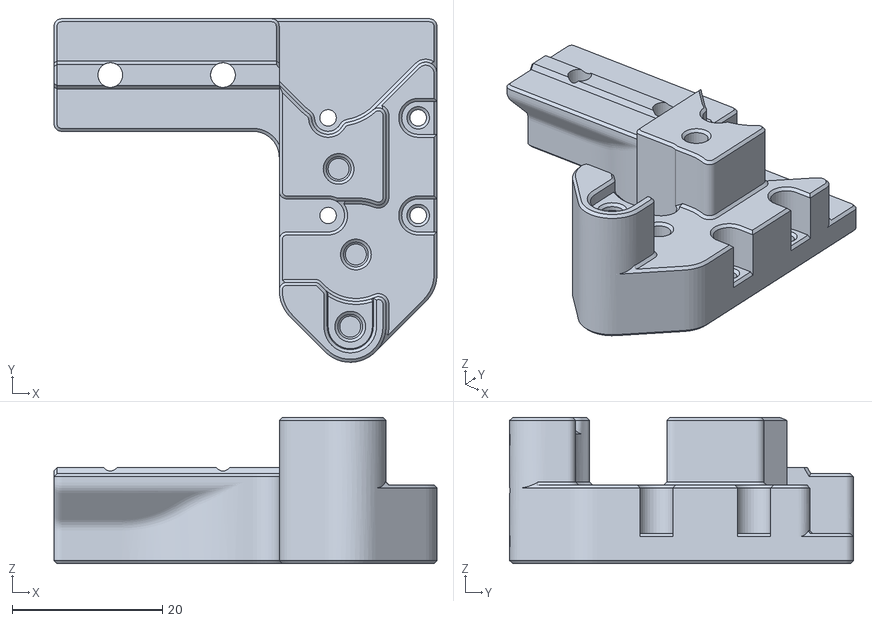
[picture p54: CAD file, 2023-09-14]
STLs/XY_Right_Lower_x2.stl
51.0 x 45.7 x 19.5

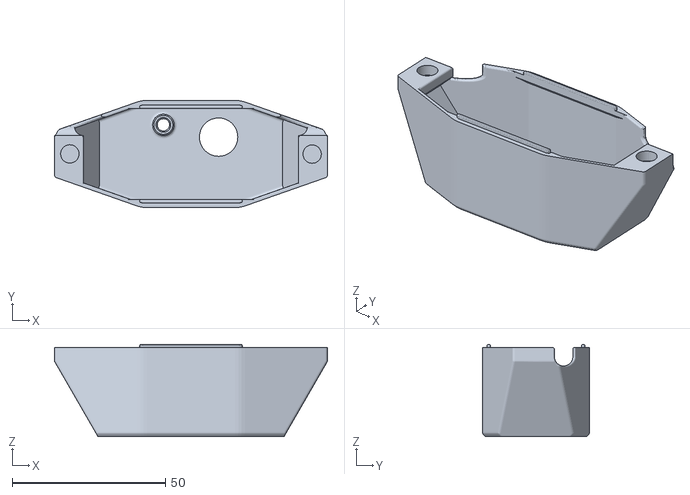
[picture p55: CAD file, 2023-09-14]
STLs/Umbilical_Box_Cover_x2.stl
89.0 x 35.0 x 30.0

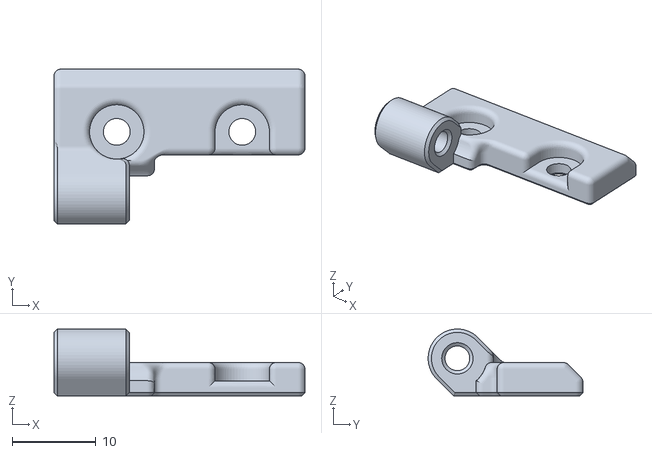
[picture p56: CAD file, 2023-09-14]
STLs/Y_Endstop_Left_x1.stl
30.0 x 18.5 x 8.00

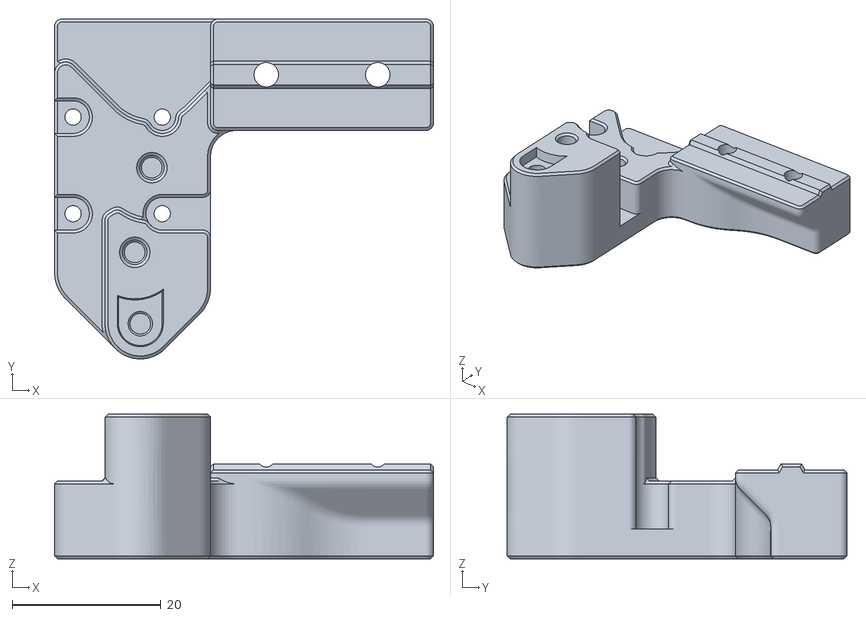
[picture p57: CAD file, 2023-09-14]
STLs/XY_Left_Lower_x2.stl
51.0 x 45.8 x 19.5

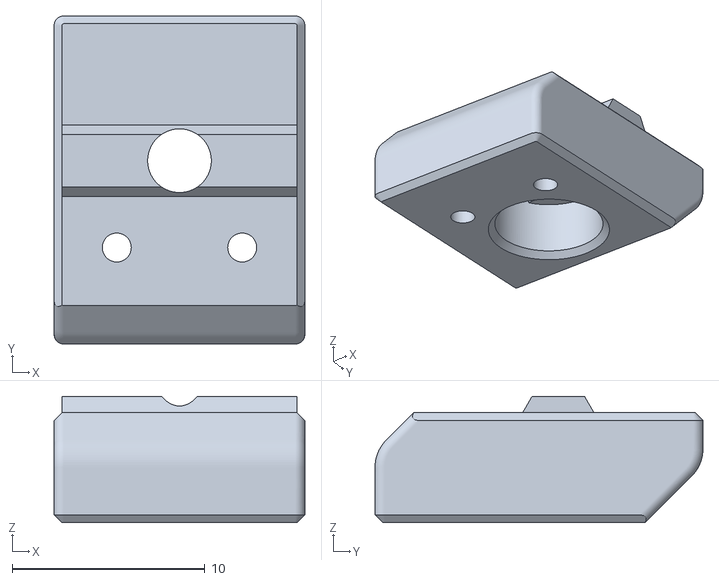
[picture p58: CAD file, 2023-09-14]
STLs/Dueling_Boops_179_Endstop_Trigger_x2.stl
13.0 x 17.0 x 6.55

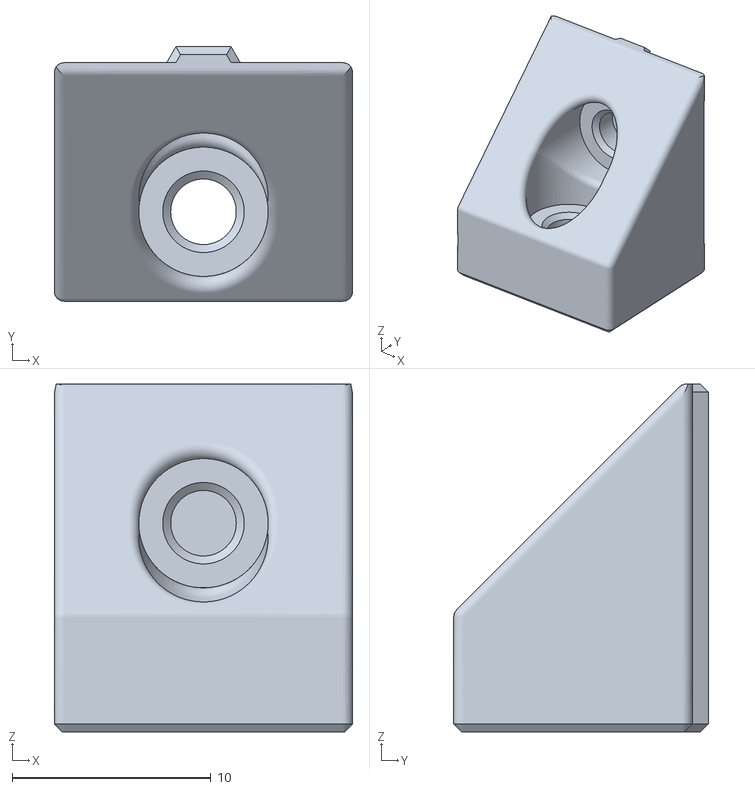
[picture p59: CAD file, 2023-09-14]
STLs/Corner_Cube_Angled_x6.stl
15.0 x 12.8 x 17.5

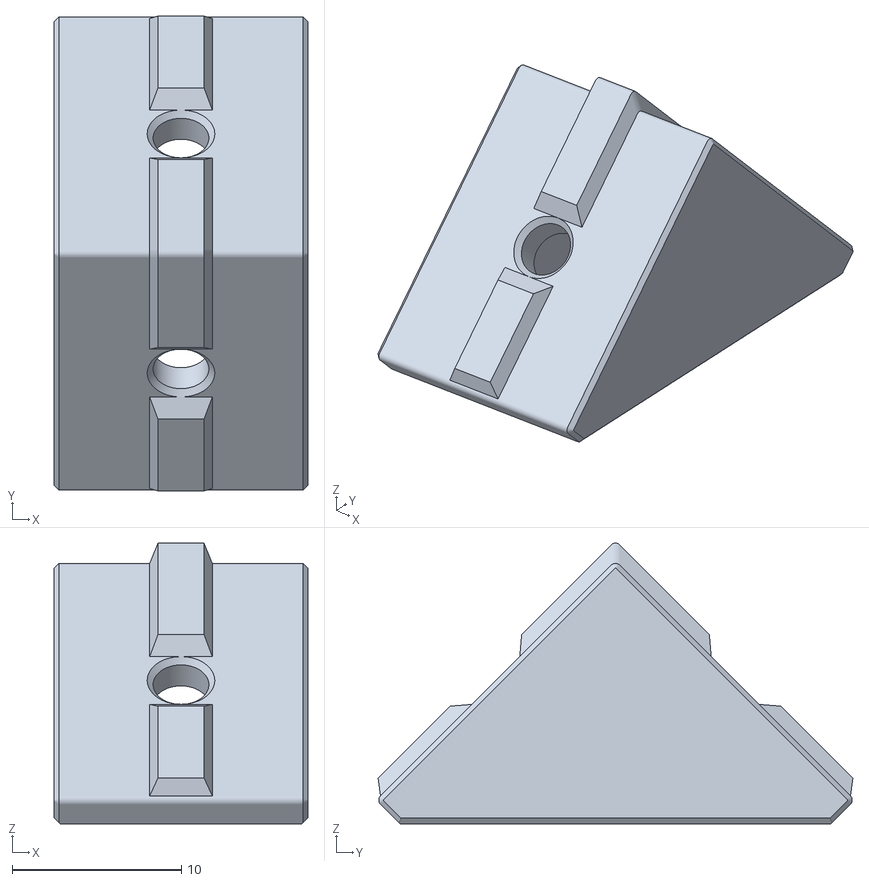
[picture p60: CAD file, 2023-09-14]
STLs/Dueling_Boops_179_Corner_x6.stl
15.0 x 28.1 x 16.6

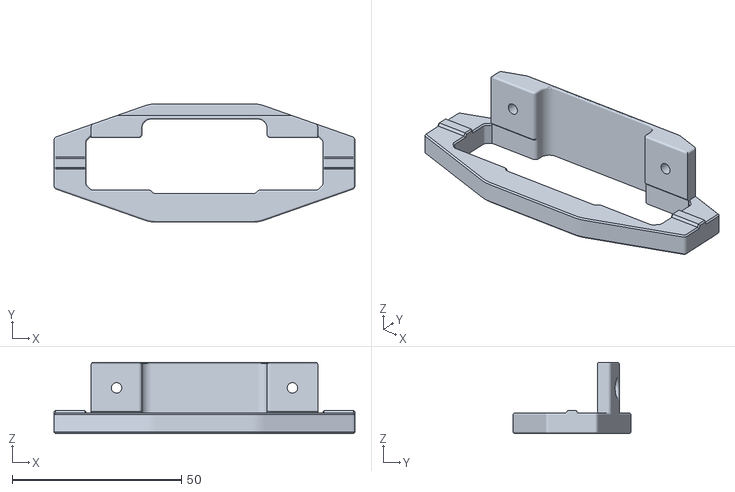
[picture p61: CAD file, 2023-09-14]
STLs/Umbilical_Box_Lower_x2.stl
89.0 x 35.0 x 21.0

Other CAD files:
src/stl/wide_bar_y.stl
STLs/AB_Left_Lower_x2.stl
STLs/Motor_Spacer_x4.stl
STLs/Front_Idler_Base_x1.stl
Archived_v1/STLs/A_Drive_Frame_Cutout_Upper_x1.stl
Archived_v1/STLs/A_Drive_Frame_Cutout_x1.stl
Archived_v1/STLs/B_Drive_Frame_Cutout_Upper_x1.stl
Archived_v1/STLs/B_Drive_Frame_Cutout_x1.stl
Archived_v1/STLs/Bottom_Corner_Front_Plus15_Mirrored_x1.stl
Archived_v1/STLs/Bottom_Corner_Front_Plus15_x1.stl
Archived_v1/STLs/Bottom_Corner_Rear_Plus15_Mirrored_x1.stl
Archived_v1/STLs/Bottom_Corner_Rear_Plus15_x1.stl
Archived_v1/STLs/Cable_Channel_15x22_60mm_Base_x6.stl
Archived_v1/STLs/Cable_Channel_15x22_60mm_Cover_x6.stl
Archived_v1/STLs/D0_T0_Front_Idler_Base_Mirrored_x1.stl
Archived_v1/STLs/D0_T0_Front_Idler_Base_x1.stl
Archived_v1/STLs/Front_Bed_Attachment_Plus15_Mirrored_x1.stl
Archived_v1/STLs/Front_Bed_Attachment_Plus15_x1.stl
Archived_v1/STLs/Front_Bed_Mount_180_x2.stl
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

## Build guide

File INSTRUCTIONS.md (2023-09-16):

## Printing Instructions

CAD exists to show what’s possible.  NOT to be an exact copy of anything except the gantry.  That’s true-to-life (to Zruncho's build), but the rest is out-of-date stuff.  If you go to the appropriate repos, you’ll have up-to-date stuff.  ZP, T0, B0.  All those are out of date within the CAD!

Parts in this repo are intentionally only the delta from other projects, so that as those projects evolve, you get the latest parts, and there's no copy/paste maintenance overhead.  Life is too short for such toil.

Really, only the gantry and the T0 idler base parts are special here.
* Standard Voron settings should be fine for all custom D0 parts: 40% infill, 4 perims, 5 top/bottom layers, 0.2mm layer height.

For other parts, use the settings specified by the respective repo:
* [BoxZero](https://github.com/zruncho3d/BoxZero)
* [TriZero](https://github.com/zruncho3d/tri-zero)
* [ZeroPanels](https://github.com/zruncho3d/ZeroPanels)
* [Boop](https://github.com/PrintersForAnts/Boop)
* [Voron V0.2](https://vorondesign.com/voron0.2)

A distinct color per gantry and per toolhead really does help keep things sane!  It's easy to get turned around when the gantry is upside-down, and when each gantry itself is flipped from the usual V0 orientation.

**NOTE**: quantities (e.g., "_x2") are for the whole printer.  So if you have two distinct-color gantries, do half of the totals for each even-quantity part with each color.

**NOTE**: Some files are missing here as STLs and CAD currently, which will be needed to match the default size, specifically:
* longer front and side skirt parts
* wider side fans
* baseplate dxf

If you're impatient, a split-move-extrude-join on the part should get you what you need quickly.

**NOTE**: All STLs are oriented with the least-visible seam in the back, and with the correct bed-plate orientation.  For most parts - AB Drive Modules and XY Joints - you can hide the seam where an extrusion will block its view.

The good news - the gantry parts are all scalable! You can start on the gantry if you want.

## Assembly Instructions

In general, the CAD should be your primary reference.  Don’t expect 100% of all screws, nuts, and heatsets to be present in CAD, though... the model is already big enough, and it leaves out some bits that should be obvious.

### Prep

* Join extrusions as needed with 20mm set screws.
* Drill 7.5mm-from-end holes for blind joints as needed, using the [V0 drill guide](https://github.com/VoronDesign/Voron-0/blob/Voron0.2r1/STLs/Tools/V0_Extrusion_Drilling_Guide_x1.STL).
* Print out a small army’s worth of no-drop nuts ([NDN](https://github.com/zruncho3d/f-zero/tree/main/STLs/NoDropNuts)s).  Size these to your extrusions.  If using a mix of LDO + MBXL, keep them apart, as the sizes will be different.  You don’t want to have to pause the build for these, or hold off on adding them everywhere because you’re running low.
* Print out extra cable channels and Wago mounts.

#### Build

It’s a cake with layers.  You make the layers independently, then you join them.  Most of the rest of the order is really up to you.

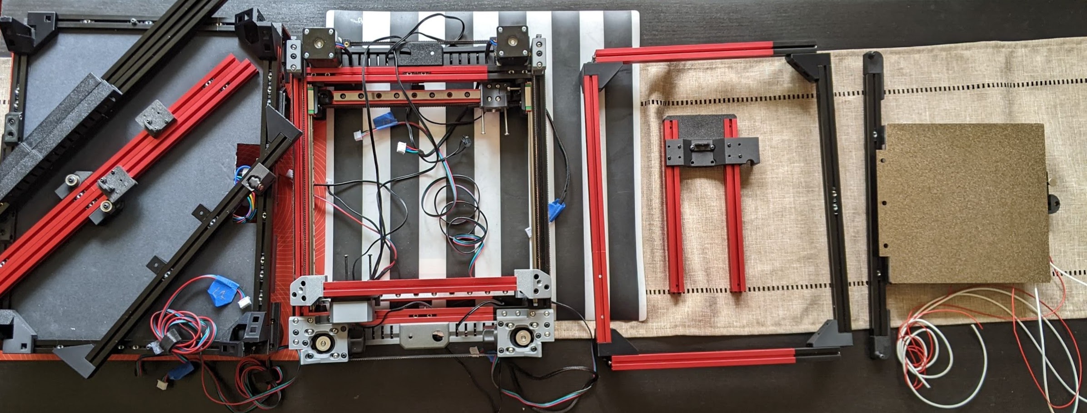
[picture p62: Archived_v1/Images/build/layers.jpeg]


In all steps, make sure to add more NDNs that you think might need!  You’ll need a lot, especially as all corners add 4-6 NDNs.

In all steps, get screws finger tight, but wait until the printer includes all parts to fully tighten all (accessible) screws.

General (order is flexible - do what you enjoy first):
* Match-fit all extrusion tabs on corners to the corresponding extrusions.  Note that extrusions have different slot widths, so be careful here.
* Build the base + skirts layer, along with lower BoxZero corners and MotoroCorners
* Mount all electrical elements and route wires
* If using BoxZero corners, build the top crown with 4 corners and 4 horizontal extrusions.  Having these corners enable a single module, even if you have a full-metal frame, is really handy for easier assembly and disassembly.
* Build and test toolheads and Boops
* Build top crown
* Build the bedframe (for T0)

XY:
* Build the complete double-gantry by itself, as a separate module.
    * Add X rails to X extrusions, ensuring alignment
    * Add Y rails to Y extrusions, ensuring alignment
    * Match-fit tabs in AB Drive Modules ("AB"s) and XY Joints ("XY"s) to extrusions (see BoxZero repo for examples of plastic curl you should see)
    * Build individual ABs and install all bearings/spacers, using CAD as a reference.
    * Build XY joints and install all bearings/spacers.  One m2 head will be tight; leave the allen in on that one, so that it's much easier to tighten when in a module.
    * Add endstop triggers and bases to the appropriate extrusions.
    * Connect two ABs into a side module, twice.
    * Connect two XYs into a Y gantry module, twice.
    * Connect AB modules to Y extrusions.
    * Attach Y gantries to the gantry frame and soft-tighten all m2s.
    * Attach toolhead carriages, loosely.  MAKE SURE THE GANTRY IS FLIPPED, relative to the usual Pandora orientation.  The screws will be in the "fall out with gravity" orientation when correct.
    * Route each of the 4 belts through the "Pandora redirection bearings" first, pushing in from the outside, then wrapping around, and pushing with an allen wrench from the inside, and back around.  You will have easy access to these belts when the verticals are not in the way.  Do all 4 of those, then add the rest of the belts and attach them to the carriages loosely.  This is the key step.
    * Add motors and align pulleys.
* Highly recommended: do all gantry electrical and config testing as a regular CoreXY on the left, and then on the right.  You want to ensure nothing is wrong with the whole XY motion stack before spending time to drop in and align the gantry.  It's motivating to have an intermediate milestone, too.  You don't even need toolheads at this point.  
* Attach toolheads and test them too.
* Optionally, configure Dual Gantry CoreXY Klipper kinematics and get T0 and T1 working.

Z:
* Build the rear Z assembly, with rails or sliders, and join it to the rear crossbar.
* Add cable channels to the rear verticals.
* Assemble rear verticals with cable carriers.
* Assemble the front verticals with T0 parts and rails or sliders.
* Add Z belts.  
* Test Z electrically, while everything is easily accessible.  You may need to slightly loosen the long front gantry screws which hold the custom T0 idler bases to make this possible. All 3 Z motors should go in the same direction, once directions are set correctly.

Main Assembly:
* Add all verticals to the base, including the rear Z frame.  Now you have a "bed of nails" layout.
* Slide in the gantry from above, matching each nail in the "bed of nails".
  * Recommended: use the joining point of the verticals as a measurement reference to get the gantry at a level height.  
  * Do an initial tightening.
* Slide on the top crown.
* Tighten all non-gantry screws.  A lot of them.
* Measure and align the gantry, so that it is as parallel as possible to the bed.  Tighten all gantry-to-frame screws (12).  106mm between bottom of top extrusions and top of gantry extrusions worked for Zruncho's build to give sufficient umbilical clearance to the top panel, but 100mm might be possible, and would make alignment super-fast with 4x 100mm extrusions and the frame upside-down temporarily.
* Add the bedframe.
* Do a complete XYZ homing cycle and maybe some z-tilt-adjust action.

Then, bask in the glory of a fully-built, Dual-Gantry CoreXY printer, one of the first of its kind.  Share it on `#dueling-zero-dev` and receive kudos.

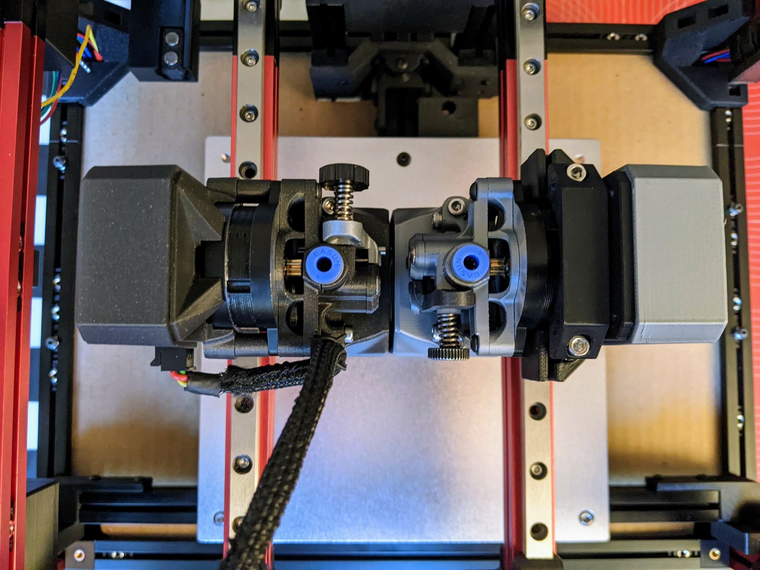
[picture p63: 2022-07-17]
Images/build/together_top.jpg

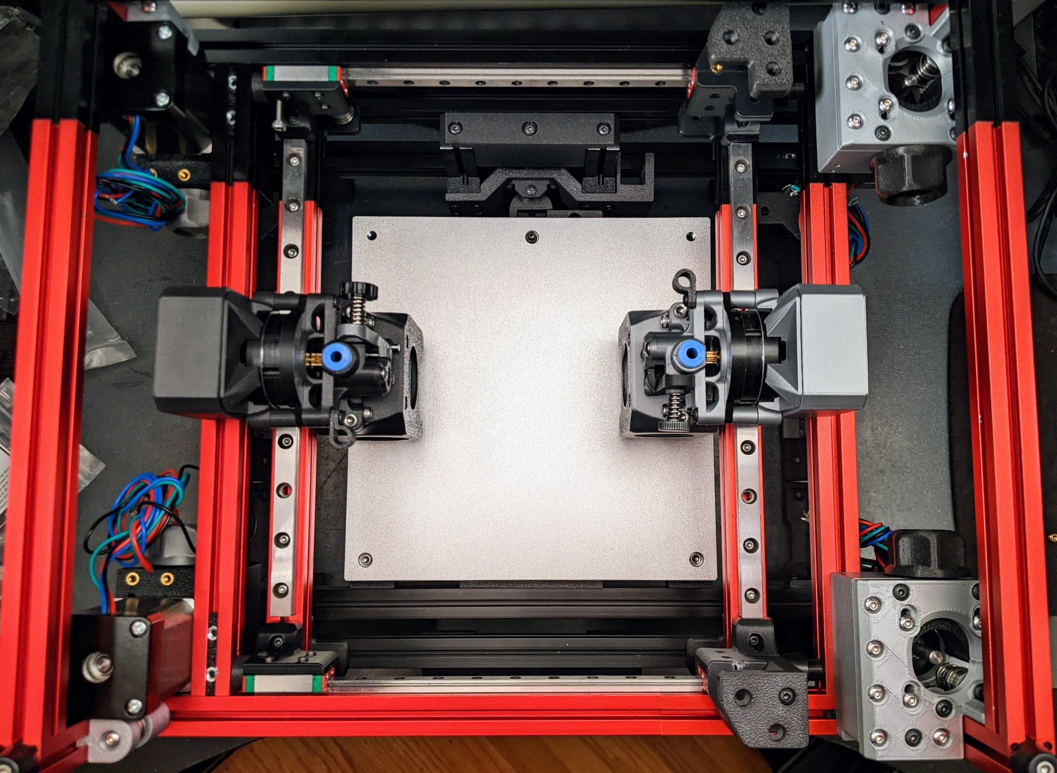
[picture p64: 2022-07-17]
Images/test_build/top.jpg

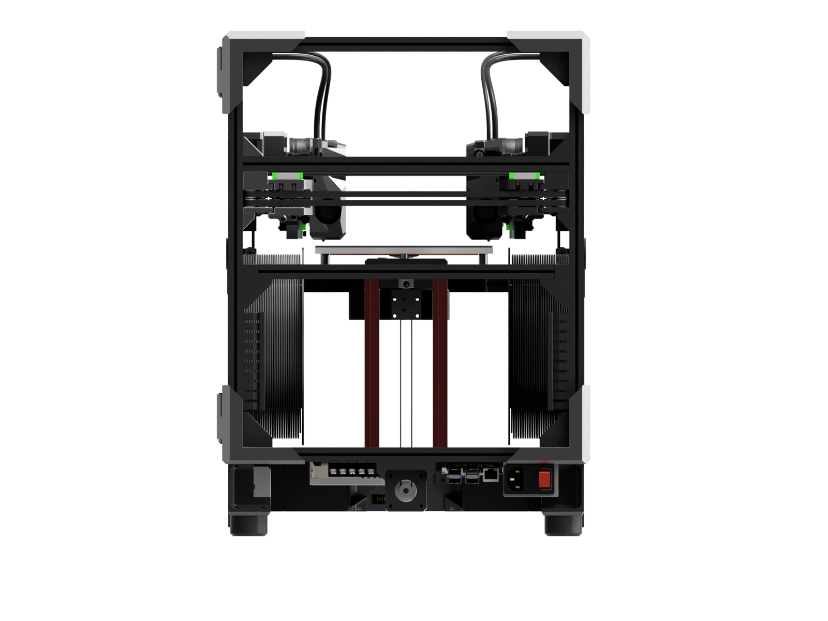
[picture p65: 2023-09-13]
Renders/Printer/rear-ortho.png

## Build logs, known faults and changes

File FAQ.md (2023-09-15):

## FAQ

### Is it still a Voron Zero?

With the v1 gantry, the answer was "Hell no":

The only printed parts shared with a regular Voron Zero were:
* 9mm spacers
* Pi mount

With the v3 gantry, the answer is "Somewhat".

The only printed parts this printer shares with a regular Voron Zero are:
* MiniSB toolhed
* Pi mount

But really...

**Hell yes!**

Because it wouldn't exist without the V0.  

Because many non-printed parts, including the frame, rails, and motors are identical, or at least similar.

So there you go... a V0 in DNA, if not in printed parts.

### Is it fun to build?

Hell no...  “Get one V0 for the pain/time/cost of two!”

**Hell yes.**  Learn a ton and get a unique and extremely rare printer type.

### Should I make one?

Hell no... "I only build printers from complete manuals."

**Hell yes!**

Everything you need is documented here in this repo.

And if you’re gonna make a printer, you might as well make it interesting.

You can even build just the left half first, then build, wire, and connect up the second gantry at your leisure.

### What’s the cost?

Probably $300+ minimum beyond a stock V0, depending on the parts you already have, with costs similar to a Double Dragon.  The second toolhead dominates the cost (hotend, extruder motor, toolhead board, fans, …), with the extra gantry adding the cost of 2 motors, bearings, rails, and new belts.  And you’ll need some new panels for the necessary widening.  Plus, you’ll need to have the extra drivers and a potentially larger power supply.

The Tri-Zero mod (if included in the build) adds cost too, as you’ll need the 3 Z motors, belts, extra extrusions, and longer rails.  

Add some money for a new, larger bed, too.

And the extra extrusions, too.

But having your very own Dual Gantry CoreXY printer - possibly the second in the world to print with two extruders in the same part: **priceless**.

### How much XY travel do I get?

With the new v3 frame size, assuming Boops are used, beyond 180x180 is possible: 184 x 194 travel.

A shorter-depth moving carriage option, like the Micron or Pandora X carriage options, would add ~8mm to each side, but would require a mount to be added for something like a Klicky.

### Can I port this to a V2-style CoreXY gantry?

Good question!

Yes, though you would lose some of the XY density, if running belts just inside of the extrusions, rather than atop the extrusions, Pandora-style.

However... maybe you won't need to.

The v3 Fusion360 CAD is heavily parametric.  Pages of parameters!  In early design, a range of parameters were actively tested, including everything needed for a V2 gantry: extrusion size, bearing size, and belt spacing.

But as of 2023-09-15, some issue with the base sketch is causing computation errors.  These are hard to debug and fix.  Stay tuned here.

### Why not just do an IDEX?

**Answering as a user**: because single-extruder prints can be faster and better without a second toolhead to drag around, and there are some unique capabilities (simultaneous different prints, full-workspace single prints) that become possible with a Dual Gantry.

**Answering as a printer-designer**: it’s a unique and interesting challenge to fit all the belts and toolheads into one gantry, especially in a way that reuses much of what’s out there.  Lots of people have described the main concept, including many years ago, but few have made it to CAD, let alone a functioning printer, let alone one that others can reproduce from a link.

**Answering as a coder**: there are some interesting - but still reasonable - 2D object interference and path-planning challenges, as well as firmware changes, to make this all work initially.  Plus, there are lots of optimizations to implement and then evaluate.

### Seems like a lotta work for a little printer, right?

Well, yes.

But it'd be even more work for a larger printer.
* It'd be impossible to rotate in your lap as you build it.
* It'd be impossible to reuse your V0 frame kit.
* It'd be impossible to store your test build in a file-folder box.

You wouldn't learn anything more.  A bigger printer would take longer to get up to temperature.  It would  have longer, harder-to-tune belts and potentially worse print quality.  It would cost more and require more energy to run.

If you don't routinely print larger objects, and especially if you do
lots of one-off small part-prototyping prints, you'll find that tiny printers rock.  Check out [3D Printers for Ants](https://3dprintersforants.com) for more examples like this one!

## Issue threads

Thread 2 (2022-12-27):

Baseplate interference with belt

zruncho3d, 2022-12-27:
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

Needs 5mm extra.  Image by Chadonka.

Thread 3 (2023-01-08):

Not an issue - Just a question...

dsred, 2023-01-08:
Dear zruncho3d,

I saw your design and find it very excellent for building an IDEX-System. Thank you for your effort!!!

I'm planning to build one just on a lager scale than 120x120mm. My question is regarding klipper: Beside adjusting all the macros, is there any additional changes in der source code of klipper necessary to get the two independent gantries running in klipper?

Thank you very much,
dsred

dsred, 2023-01-11:
Dear zruncho3d,

I properly should have done this before but after reading all your documentation including software-readme most my questions are clear now.

To run klipper you will need to work with this repository: https://github.com/Tircown/klipper-zruncho
And the need of two skr boards seems also to arise from current klipper limitations.

Do you know if this implementations will find they way into the official klipper branch at some point. Is there still development going on here?

Thank youvery much,
dsred

zruncho3d, 2023-01-13:
Hi.  FWIW, I don't know anyone who's looking to build one at the 120x120 size; it really makes more sense in the 170x170-ish range, and honestly I should increase the width by 20mm by default so that you can get closer or to the full 170-180 width of a Prusa Mini or K3 bed.

Re: Klipper code - it's really just the one-file change required to move two gantries with T0 and T1 commands and have them home.  Use this branch, until further notice:
https://github.com/zruncho3d/klipper-orig/commits/dual_gantry_unsquashed

Tircown had made some changes with unanticipated side effects and I don't recall if the branch you reference is that one.  I recently rebased this branch on the latest kilpper and it all worked fine, as all changes are to the one kinematics file.

**Run whatever you've got;** the beauty of Klipper is that it doesn't matter what drivers, or number of them, you use.  I've been meaning to switch to an Octo Pro recently to have the possibility of later deploying RRF support.  That would be one board with the CAN side built in, so it'd be pretty clean to wire, at least as clean as you can get without going to gantry boards.  EBBs are my favorite toolboard because of easy DFU flashing and larger connectors and low price, and EBB36 should be fine here; just don't print the shrouds for square boards like mine (EBB42).

Re: official Klipper - Kevin's policy is to prioritize patches for integration with higher numbers of printers affected.  That's fair, and this isn't a board-value patch 😄 .    In the long run though, I think that policy is actively harmful for code like this which could make Klipper the best choice for a kind of kinematics.  But the good news is that it doesn't matter what Kevin does.  It's just one file, thanks to great work by Tircown.  And I know Tircown would love to improve that code for mergeability over time too.  If we get a bunch of Dueling Zeros, I'm sure Kevin would be more receptive to inclusion, and I'd love to see that in the release notes someday, especially because the number of people whose code would be broken is very low.

So ... are you gonna build one, and be the first in the world beyond the original to get one working? 😄

jeremiahvpratt, 2023-02-09:
Hey zruncho! Is this still the recommended branch for klipper? Also, [the klipper firmware section](https://github.com/zruncho3d/DuelingZero/blob/main/SOFTWARE.md#klipper-patch-for-dual-gantry-corexy) of the software page is currently missing a link to the dual gantry firmware repo (which is understandable if the main branch is unstable and you still recommend this alternative)

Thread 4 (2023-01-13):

High-side XY joints (both parts) missing in STLs dir

zruncho3d, 2023-01-13:
Workaround: grab from CAD

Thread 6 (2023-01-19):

XY_Joint_Strut_Mount_x1.stl not oriented correctly for printing

zruncho3d, 2023-01-19:

madejackson, 2023-01-19:
Wrong direction as well for:
- Top_Corner_Plus15_Plus30.stl
- Top_Corner_Plus15_Plus30_Mirrored.stl
- High_Side_X_Carriage_x1.stl

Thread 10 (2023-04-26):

BOM

TekuSP, 2023-04-26:
Hey,

I appreciate parts page, but I would love to have full BOM.
I want to expand Z axis by 100mm so full BOM would help me with that.

Thank you.

M4dMike, 2023-06-01:
Same here

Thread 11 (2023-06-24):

Klipper support

PhilsWorksop, 2023-06-24:
Hi,

I have built a dueling zero and am now working on Klipper,
i am as far as the config, but when i copy yours it always says "Error loading kinematics 'dualgantry_corexy'".
And i can`t find these kinematics on the klipper documentation ?
Where/ how do i get my klipper to recognize these kinematics?
Thanks in advance,

Phil

rbricheno, 2024-01-07:
That's described here:

https://github.com/zruncho3d/DuelingZero/blob/main/SOFTWARE.md

There's a fork of Klipper which contains the new kinematics here:

https://github.com/zruncho3d/klipper/tree/dual_gantry_main

The specific file of interest is this:

https://github.com/zruncho3d/klipper/blob/dual_gantry_main/klippy/kinematics/dualgantry_corexy.py

When I tested this a couple of months ago, I found that I was able to simply copy the one file with the new kinematics from that fork into a normal installation of klippy and it worked (ghetto rebase!).

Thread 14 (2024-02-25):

CAN Bus Setup for Dual Hotend 3D Printer

Nico4589, 2024-02-25:
Hello, I have come across your project, and it is quite intriguing. I am currently in the process of developing a printer with a dual hotend, and I am interested in implementing CAN bus communication for the two printing heads, as you have done. Could you kindly provide a comprehensive guide on the electrical connection of the bus cables and the configuration of communication channels? While I have reviewed your configurations for the right and left sides, I am struggling to comprehend the underlying logic of its functionality. Your assistance on this matter would be greatly appreciated. Thank you.

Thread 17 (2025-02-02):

Dual gantry for Cartesian kinematics

Dan3dp, 2025-02-02:
hi zruncho3d,

I'm building a dual gantry 3D printer. However, unlike your doeling_zero, my setup uses Cartesian kinematics instead of CoreXY.

Is there any chance you could release a dualgantry_cartesian.py?

I've been struggling to modify your original dualgantry_corexy.py.

Since I'm not familiar with Python, I haven't managed to achieve usable results.

Thanks in advance for replying.

Regards,
Dan

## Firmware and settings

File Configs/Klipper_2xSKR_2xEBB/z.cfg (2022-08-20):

[mcu z]
serial: /dev/serial/by-id/usb-Klipper_rp2040_45503571270F6A78-if00
restart_method: command

[stepper_z]
step_pin: z:gpio11
dir_pin: !z:gpio10
enable_pin: !z:gpio12
microsteps: 64
rotation_distance: 32
endstop_pin: ^z:gpio4
# endstop_pin: tmc2209_stepper_x:virtual_endstop
# homing_retract_dist: 0
position_endstop: 0
position_max: 125
position_min: -1.0
homing_speed: 10

[tmc2209 stepper_z]
uart_pin: z:gpio9
tx_pin: z:gpio8
uart_address: 0
run_current: 0.8
hold_current: 0.8
stealthchop_threshold: 500
# diag_pin: ^gpio4
# driver_SGTHRS: 100

[stepper_z1]
step_pin: z:gpio6
dir_pin: z:gpio5
enable_pin: !z:gpio7
microsteps: 64
rotation_distance: 32
#endstop_pin: ^z:gpio3
# endstop_pin: tmc2209_stepper_y:virtual_endstop
# homing_retract_dist: 0
#position_endstop: 0
#position_max: 235
#homing_speed: 50

[tmc2209 stepper_z1]
uart_pin: z:gpio9
tx_pin: z:gpio8
uart_address: 2
run_current: 0.8
hold_current: 0.8
stealthchop_threshold: 500
diag_pin: ^z:gpio3
driver_SGTHRS: 100

[stepper_z2]
step_pin: z:gpio19
dir_pin: z:gpio28
enable_pin: !z:gpio2
microsteps: 64
rotation_distance: 32
# endstop_pin: ^gpio25
# position_endstop: 0
#endstop_pin: probe:z_virtual_endstop
#position_min: -2.0
#position_max: 250
#homing_speed: 12

[tmc2209 stepper_z2]
uart_pin: z:gpio9
tx_pin: z:gpio8
uart_address: 1

run_current: 0.8
hold_current: 0.8
stealthchop_threshold: 500

# [extruder]
# step_pin: gpio14
# dir_pin: !gpio13
# enable_pin: !gpio15
# microsteps: 16
# rotation_distance: 33.500
# nozzle_diameter: 0.4
# filament_diameter: 1.75
# heater_pin: gpio23
# sensor_type: EPCOS 100K B57560G104F
# sensor_pin: gpio27
# control: pid
# pid_Kp: 22.2
# pid_Ki: 1.08
# pid_Kd: 114
# min_temp: 0
# max_temp: 300
# max_extrude_cross_section:2

# [tmc2209 extruder]
# uart_pin: gpio9
# tx_pin: gpio8
# uart_address: 3
# run_current: 0.650
# hold_current: 0.500
# stealthchop_threshold: 999999

# [filament_switch_sensor runout_sensor]
# switch_pin: ^gpio16
# pause_on_runout: True

# [filament_motion_sensor smart_sensor]
# switch_pin: ^gpio16
# detection_length: 2.5

[heater_bed]
heater_pin: z:gpio29
##  See https://www.klipper3d.org/Config_Reference.html#common-thermistors for additional options
sensor_type: Generic 3950
#sensor_type: EPCOS 100K B57560G104F
sensor_pin: z:gpio26
control: pid
pid_Kp: 54.027
pid_Ki: 1.464
pid_Kd: 297.33
min_temp: 0
max_temp: 130

# [fan]
# pin: gpio17

# [heater_fan hotend_fan]
# pin: gpio18
# heater: extruder
# heater_temp: 50.0

# [heater_fan controller_fan]
# pin: gpio20
# heater: heater_bed
# heater_temp: 45.0

# [printer]
# kinematics: cartesian
# max_velocity: 500
# max_accel: 3000
# max_z_velocity: 25
# max_z_accel: 30

#[bltouch]
#sensor_pin: gpio22
#control_pin: gpio29

# [neopixel board_rgb]
# pin: gpio24
# chain_count: 1
# color_order: GRB
# initial_RED: 0.3
# initial_GREEN: 0.3
# initial_BLUE: 0.3

########################

#####################################################################
# 	Probe
#####################################################################

[probe]
##	This probe is not used for Z height, only Leveling
##	Z_MAX on mcu_z
##	If your probe is NO instead of NC, add change pin to !z:P0.10
#pin: ^z:P0.10
pin: ^EBBCan:PA5
#pin: ^!toolhead:gpio12  # ES0 Test

# Values for ZeroClick
# Determined from CAD.
# ZeroClick probe position is 7mm from edge.  
# Magnet center is 5mm from edge.
# 9mm between magnet centers.  
# 4.5mm offset + 5mm - 7 --> 2.5mm offset from center of ZeroClick
# 20.95mm X offset from center of toolhead to center of ZeroClick; 21 - 2.5 is -18.5 X offset
# From CAD: 18.2mm Y offset.
x_offset: -18.5
y_offset: -18.2

# Reduce the Z offset if the nozzle hits early, with z>0.5 with a 0.5-thick business car.
# Increase the Z offset if the nozzle is not low enough at Z=0.5 with a card below.
z_offset: 10.4


speed: 20.0
lift_speed: 50.0
samples: 3
samples_result: median
sample_retract_dist: 1.0
# Was: 0.006
samples_tolerance: 0.021
samples_tolerance_retries: 3

[safe_z_home]
# ##  XY Location of the Z Endstop Switch
# ##  Update -10,-10 to the XY coordinates of your endstop pin 
# ##  (such as 157,305) after going through Z Endstop Pin
# ##  Location Definition step.
# Previously, was 131, 28, with the right-side endstop.
#home_xy_position: 131, 28
home_xy_position: 60, 168.4
speed:100
z_hop:4

[z_tilt]
#z_positions:
#   A list of X,Y coordinates (one per line; subsequent lines
#   indented) describing the location of each bed "pivot point". The
#   "pivot point" is the point where the bed attaches to the given Z
#   stepper. It is described using nozzle coordinates (the XY position
#   of the nozzle if it could move directly above the point). The
#   first entry corresponds to stepper_z, the second to stepper_z1,
#   the third to stepper_z2, etc. This parameter must be provided.
# Original ones:
# z_positions:
#     164, 12
#     -44, 12
#     60, 135
# Original (2022-02-27):
# z_positions:
#     214, 12
#     -94, 12
#     60, 135
# Modified (2022-02-27+):
# z_positions:
#     218.24, 12
#     -96.76, 12
#     60.74, 135
# Before, Was:
#z_positions:
#     214, 12
#     -94, 12
#     60, 135
z_positions:
     229, 12
     -109, 12
     60, 185


#points:
#   A list of X,Y coordinates (one per line; subsequent lines
#   indented) that should be probed during a Z_TILT_ADJUST command.
#   Specify coordinates of the nozzle and be sure the probe is above
#   the bed at the given nozzle coordinates. This parameter must be
#   provided.

# Points for ZeroClick
points:
    25, 5
    155, 5
    90, 140

#speed: 50
#   The speed (in mm/s) of non-probing moves during the calibration.
#   The default is 50.
speed: 200

#horizontal_move_z: 5
#   The height (in mm) that the head should be commanded to move to
#   just prior to starting a probe operation. The default is 5.
horizontal_move_z: 15

#retries: 0
#   Number of times to retry if the probed points aren't within
#   tolerance.
retries: 4

#retry_tolerance: 0
#   If retries are enabled then retry if largest and smallest probed
#   points differ more than retry_tolerance. Note the smallest unit of
#   change here would be a single step. However if you are probing
#   more points than steppers then you will likely have a fixed
#   minimum value for the range of probed points which you can learn
#   by observing command output.
retry_tolerance: 0.01

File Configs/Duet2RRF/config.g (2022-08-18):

; CoreXYUV Config, with 2 Toolheads defined
; X stepper: L2
; Y stepper: L1
; Z stepper: R1
; E0 stepper: R2

; General preferences
M575 P1 S1 B57600                              ; enable support for PanelDue
G90                                            ; send absolute coordinates...
M83                                            ; ...but relative extruder moves
M550 P"duelingzero"                            ; set printer name

; Network
M552 S1                                        ; enable network
M586 P0 S1                                     ; enable HTTP
M586 P1 S0                                     ; disable FTP
M586 P2 S0                                     ; disable Telnet

; Printer
M669 K8 ; switch to CoreXYUV mode
M569 P0 S0                                     ; physical drive 0 goes forwards
M569 P1 S1                                     ; physical drive 1 goes forwards
M569 P2 S0                                     ; physical drive 2 goes forwards
M569 P3 S1                                     ; physical drive 3 goes forwards
M584 X0 Y1 U2 V3 E4                            ; set drive mapping (CoreXYUV); E4 is a dummy but needed for tool defn's later.
M350 X16 Y16 U16 V16 I1                        ; configure microstepping with interpolation
M92 X80.00 Y80.00 U80.00 V80.00                ; set steps per mm
M566 X900.00 Y900.00 U900.00 V900.00           ; set maximum instantaneous speed changes (mm/min)
M203 X6000.00 Y6000.00 U6000.00 V6000.00       ; set maximum speeds (mm/min)
M201 X1000.00 Y1000.00 U1000.00 V1000.00       ; set accelerations (mm/s^2)
M906 X650 Y650 U650 V650 I30                   ; set motor currents (mA) and motor idle factor in per cent
M84 S30                                        ; Set idle timeout

; Axis Limits
M208 S1 X0 Y0 U0 V0                               ; set axis minima
M208 S0 X120 Y160 U120 V160                       ; set axis maxima

; Endstops
M574 X1 S1 P"xstop"                            ; configure switch-type (e.g. microswitch) endstop for low end on X via pin xstop
M574 Y2 S1 P"ystop"                            ; configure switch-type (e.g. microswitch) endstop for high end on Y via pin ystop
M574 U2 S1 P"zstop"                            ; configure switch-type (e.g. microswitch) endstop for high end on U via pin zstop
M574 V1 S1 P"e0stop"                            ; configure switch-type (e.g. microswitch) endstop for low end on V via pin ystop

;M574 Z1 S2                                     ; configure Z-probe endstop for low end on Z

; Z-Probe
;M558 P1 C"zprobe.in" H5 F120 T6000             ; set Z probe type to unmodulated and the dive height + speeds
;G31 P500 X0 Y0 Z2.5                            ; set Z probe trigger value, offset and trigger height
;M557 X15:120 Y15:160 S20                       ; define mesh grid

; Heaters
M308 S0 P"bedtemp" Y"thermistor" T100000 B4138 ; configure sensor 0 as thermistor on pin bedtemp
M950 H0 C"bedheat" T0                          ; create bed heater output on bedheat and map it to sensor 0
M307 H0 B1 S1.00                               ; enable bang-bang mode for the bed heater and set PWM limit
M140 H0                                        ; map heated bed to heater 0
M143 H0 S120                                   ; set temperature limit for heater 0 to 120C
M308 S1 P"e0temp" Y"thermistor" T100000 B4138  ; configure sensor 1 as thermistor on pin e0temp
M950 H1 C"e0heat" T1                           ; create nozzle heater output on e0heat and map it to sensor 1
M307 H1 B0 S1.00                               ; disable bang-bang mode for heater  and set PWM limit
M143 H1 S280                                   ; set temperature limit for heater 1 to 280C

; Fans
M950 F0 C"fan0" Q500                           ; create fan 0 on pin fan0 and set its frequency
M106 P0 S0 H-1                                 ; set fan 0 value. Thermostatic control is turned off
M950 F1 C"fan1" Q500                           ; create fan 1 on pin fan1 and set its frequency
M106 P1 S1 H1 T45                              ; set fan 1 value. Thermostatic control is turned on

; Tools
; https://docs.duet3d.com/User_manual/Reference/Gcodes#m563-define-or-remove-a-tool
; Note: Axes are mapped in the order XYZUVWABC, where X=0, Y=1, Z=2, U=3 etc, not by driver number.
M563 P0 D0 H1 F0 S"left"                       ; define tool 0
G10 P0 X0 Y0                                   ; set tool 0 axis offsets
G10 P0 R0 S0                                   ; set initial tool 0 active and standby temperatures to 0C

M563 P1 D0 H1 F0 X3 Y4 S"right"                ; define tool 1 motion;
G10 P1 U0 V0                                   ; set tool 1 axis offsets
G10 P1 R0 S0                                   ; set initial tool 1 active and standby temperatures to 0C

; Custom settings are not defined

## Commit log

2022-06-26 THE TOOLHEADS ARE DANCING; all cases handled now
2022-07-22 refactor: Extract toolhead tests to separate file
2022-07-23 Add stl examples used for code tests
    [cylinder_2_layer.stl, square_2_layer.stl, wide_bar_x.stl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]
2022-07-26 README.md: Add panel orders
    Also:
    * do a few more terminology tweaks.
    * show 'souvenir' extrusions
    * consistent usage of G-code
    * add 'layers' pic
    * more FAQ entries
2022-07-26 Add baseplate DXF
    [baseplate.dxf]
2022-07-27 Add DESIGN.md part 1
    Covers gantry parts with pics and explanation
2022-07-27 Add first batch of STLs
    [A_Drive_Frame_Cutout_Upper_x1.stl, A_Drive_Frame_Cutout_x1.stl, B_Drive_Frame_Cutout_Upper_x1.stl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]
2022-07-28 DESIGN.md: Add part 2
    Covers Z motion, frame, and other bits
2022-08-15 Reference bed-fraction ssheet + update software docs
2022-08-18 Add more STLs
    [High_Side_Belt_Grab_Mirrored_x2.stl, High_Side_Belt_Grab_x2.stl, High_Side_Top_Strap_x1.stl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]
2022-08-18 Add .step CAD export
2022-08-18 Add RRF sample config
    [config.g, homeall.g, tfree0.g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]
2022-08-20 Add f3z cad link to Gdrive :shrug:
2022-08-20 Add Klipper configs
    [ebb42-left.cfg, ebb42-right.cfg, fluidd.cfg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]
2022-08-21 Add like to multi-extrusion gist
2023-08-31 DXF - extend baseplate holes for belts by 5mm
    [baseplate.dxf]
2023-09-14 Add v3 STLs
    [AB_Left_Lower_x2.stl, AB_Left_Upper_x2.stl, AB_Right_Lower_x2.stl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]
2023-09-14 Add back moved v1 STLs
    [A_Drive_Frame_Cutout_Upper_x1.stl, A_Drive_Frame_Cutout_x1.stl, B_Drive_Frame_Cutout_Upper_x1.stl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]
2023-09-15 Add updated CAD
2023-09-15 More sample build and upgrade notes
2023-09-15 Note STL orientation default
